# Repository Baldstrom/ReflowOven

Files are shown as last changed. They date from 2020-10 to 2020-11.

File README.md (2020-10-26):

# ReflowOven
A reflow oven controller designed in KiCAD, by Jaden Bottemiller

This project is designed to use an STM32 ARM Cortex-M4 microcontroller. 

All onboard devices interface to the microcontroller using I2C (with the exception of the SD Card Slot, which uses SPI). Also has a CAN interface, USB 2.0, and SWD. Features four seven segment displays, three buttons, and a rotary encoder with a custom logic circuit that interfaces with an I2C binary up/down counter to increment, decrement, and maintain accuracy of the relative position of the encoder.

Here is a rendering of the board with all of the parts modelled.
Some models from online resources or default in KiCAD, but many were made by me in Solidworks.

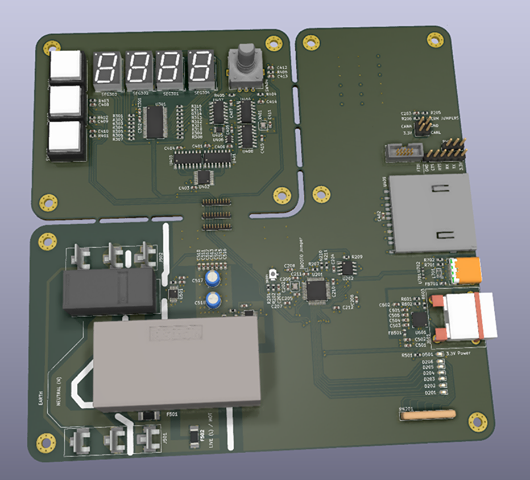
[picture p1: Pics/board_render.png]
Image of Board


The user interface portion of the board is able to be cut off so that it can be placed anywhere in a mechanical chassis for ease of construction.

Here is the board as seen by default in the KiCAD PCBnew Software.

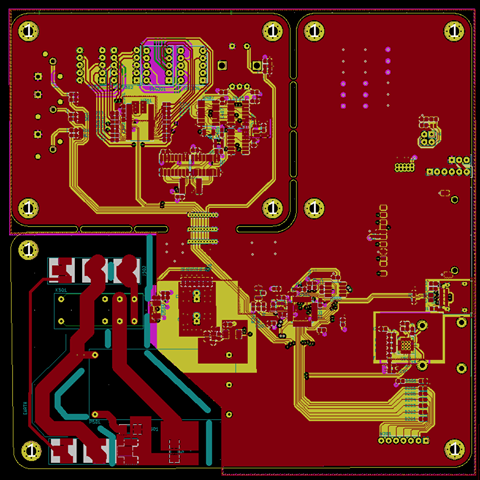
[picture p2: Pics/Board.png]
Image of PCBnew Render


A PDF of the Schematic Sheets can be found [here](https://github.com/Baldstrom/ReflowOven/blob/main/PDFs/ReflowOven.pdf).

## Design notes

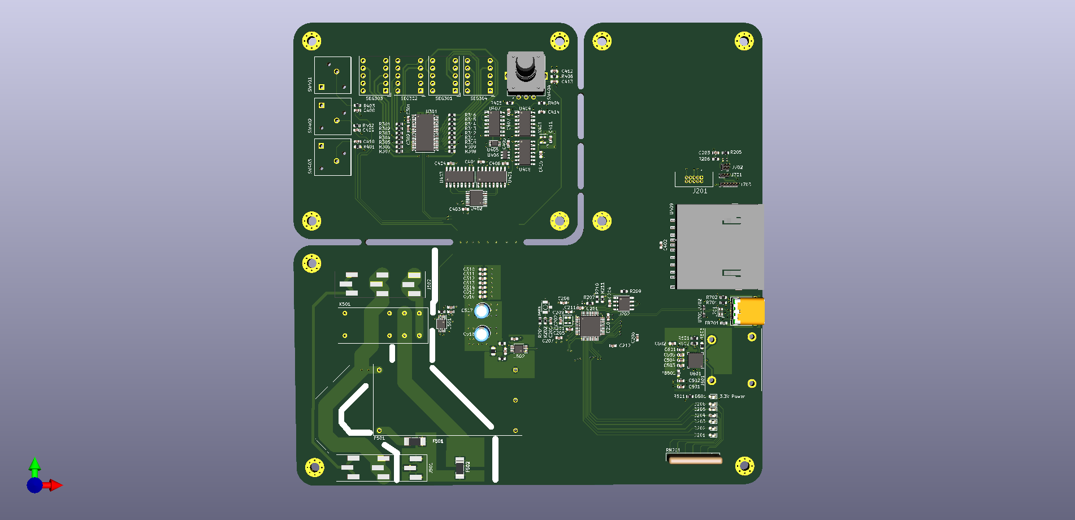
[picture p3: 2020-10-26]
Pics/ReflowOven.png

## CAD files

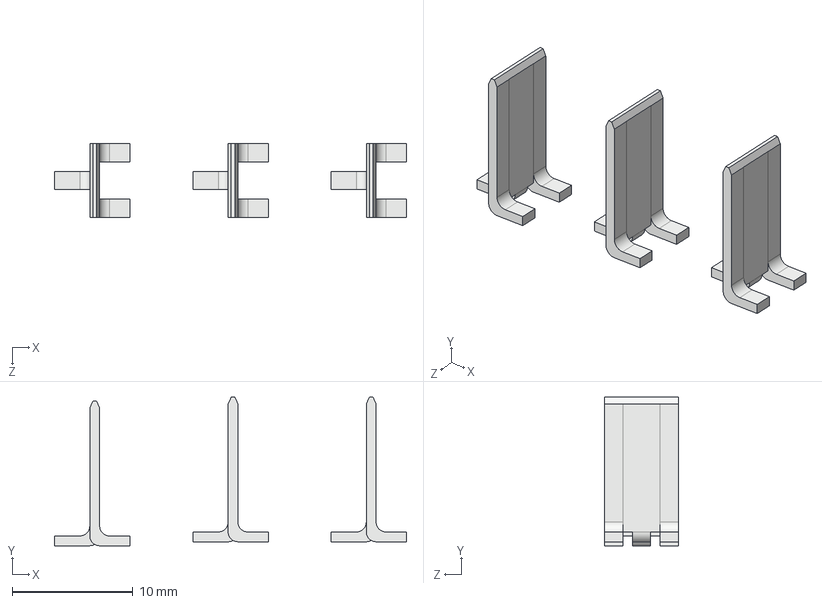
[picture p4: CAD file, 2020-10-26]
3D-Models/spade_connector_assy.STEP
29.1 x 12.3 x 6.10 mm
4928TR x 3

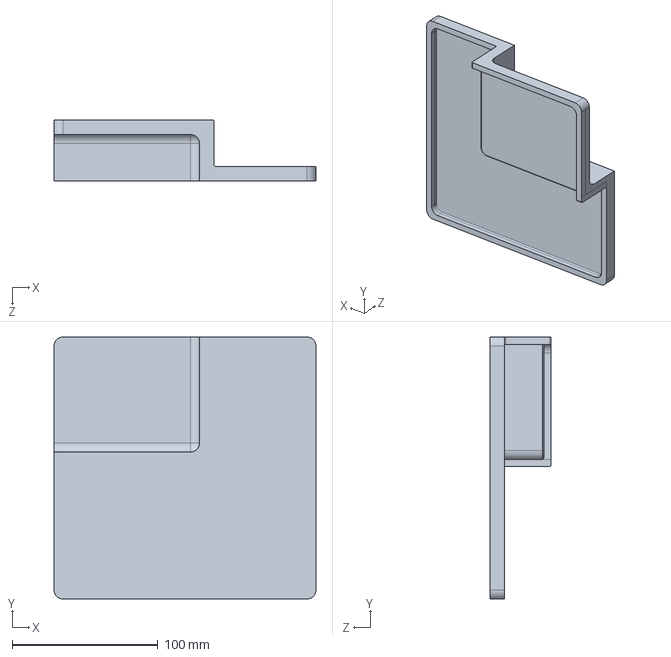
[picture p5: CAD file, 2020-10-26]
CAD/Chassis-Upper.SLDPRT
180.0 x 180.0 x 42.0 mm

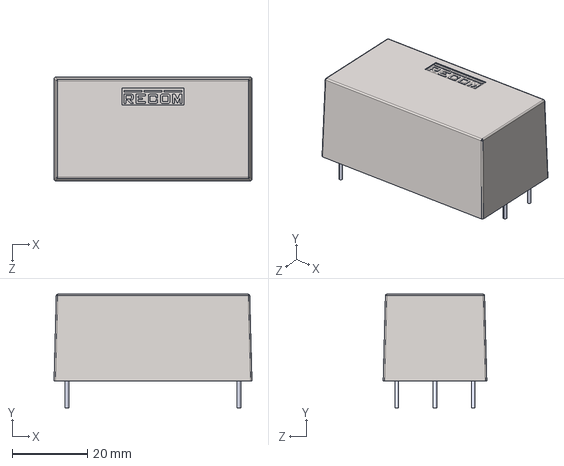
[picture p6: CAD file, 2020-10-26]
3D-Models/277.stp
52.7 x 30.2 x 27.6 mm

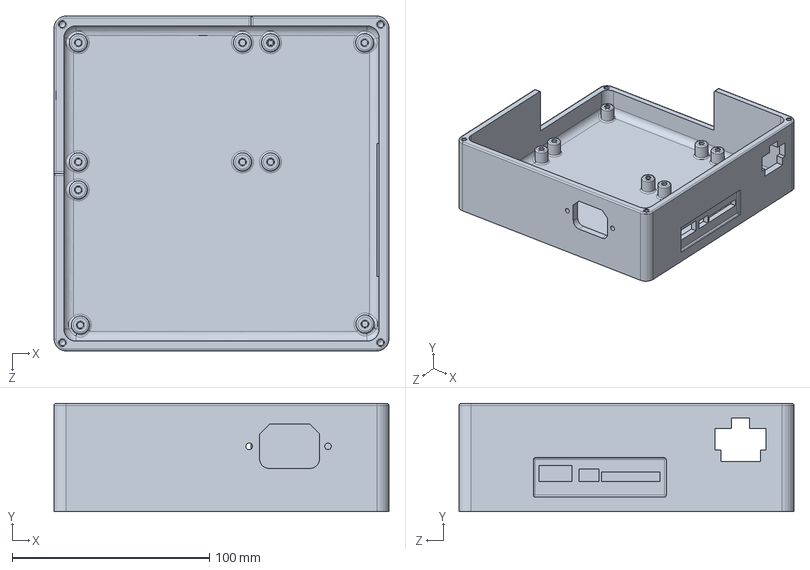
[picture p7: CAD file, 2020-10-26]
CAD/Chassis-Lower.SLDPRT
170.0 x 55.0 x 170.0 mm

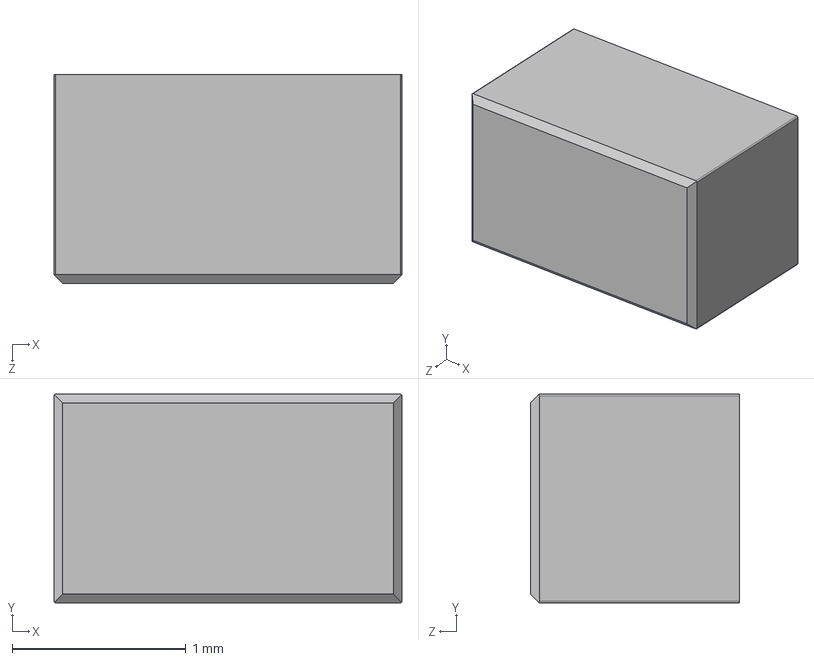
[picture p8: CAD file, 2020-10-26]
3D-Models/Choke.stl.STEP
2.00 x 1.20 x 1.20 mm

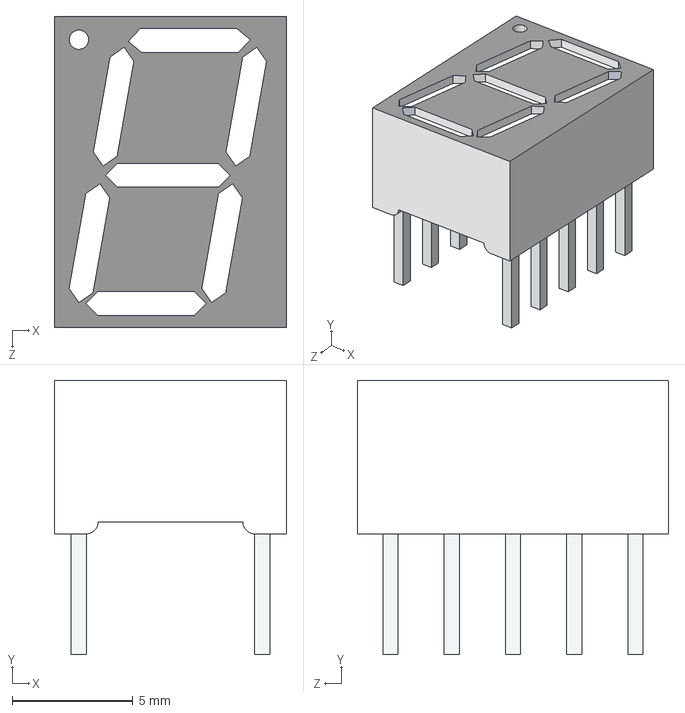
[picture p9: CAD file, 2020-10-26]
3D-Models/7seg.STEP
9.63 x 11.4 x 12.9 mm

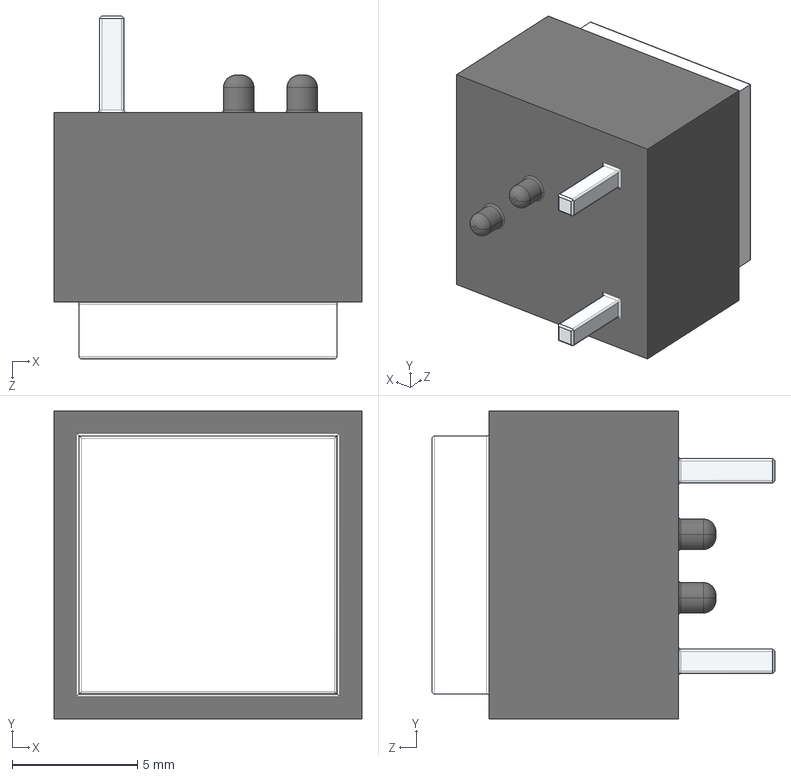
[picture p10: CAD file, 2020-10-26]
3D-Models/CKN4078-ND.STEP
12.3 x 12.3 x 13.7 mm

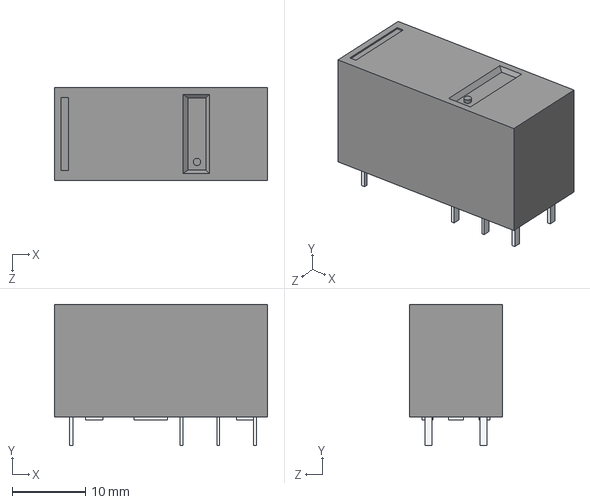
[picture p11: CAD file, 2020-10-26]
3D-Models/G5RL_U1_E.STEP
29.0 x 19.2 x 12.7 mm

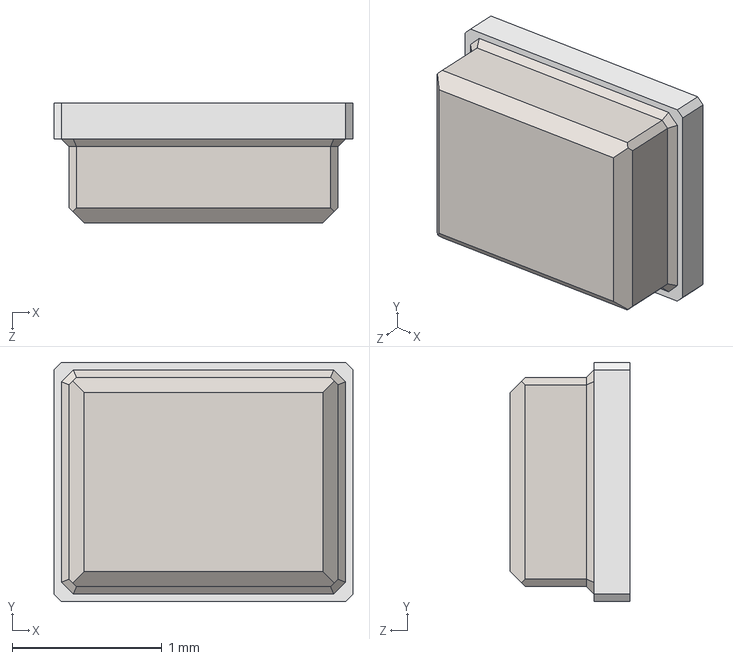
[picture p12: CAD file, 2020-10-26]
3D-Models/KC2016Z.stp
2.00 x 1.60 x 0.8 mm

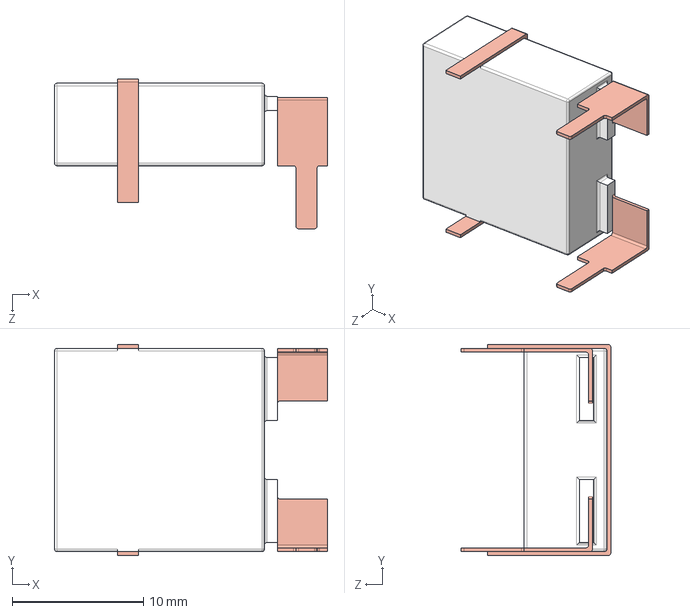
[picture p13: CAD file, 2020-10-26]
3D-Models/PRT-13612.stp
20.8 x 16.1 x 11.4 mm

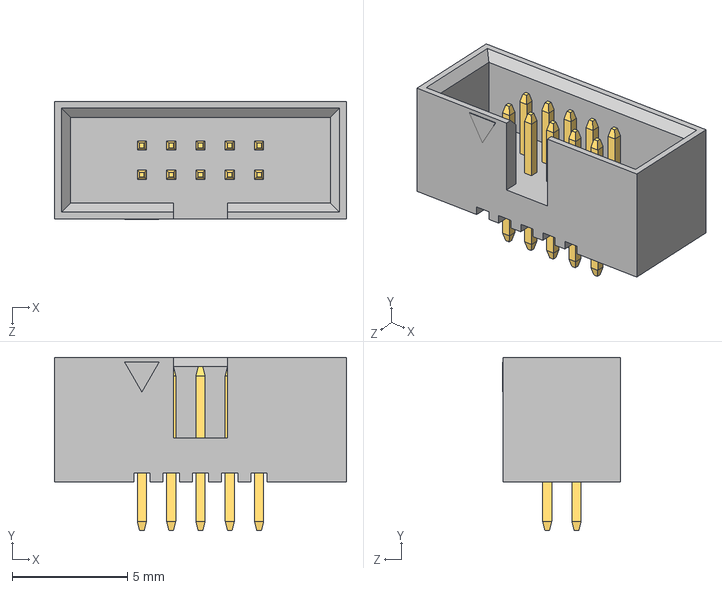
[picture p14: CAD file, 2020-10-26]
3D-Models/3220-10-0100.stp
12.7 x 7.50 x 5.13 mm

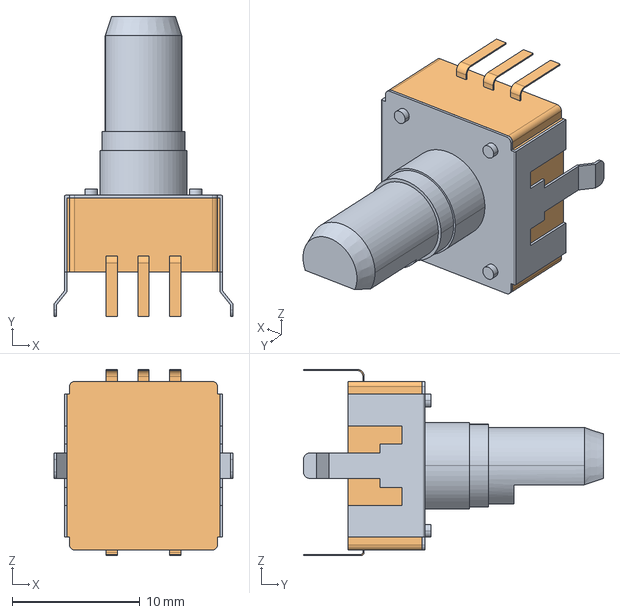
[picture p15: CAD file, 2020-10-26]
3D-Models/en12-hs22af20.stp
14.0 x 23.5 x 14.6 mm
BM-427
BM-428

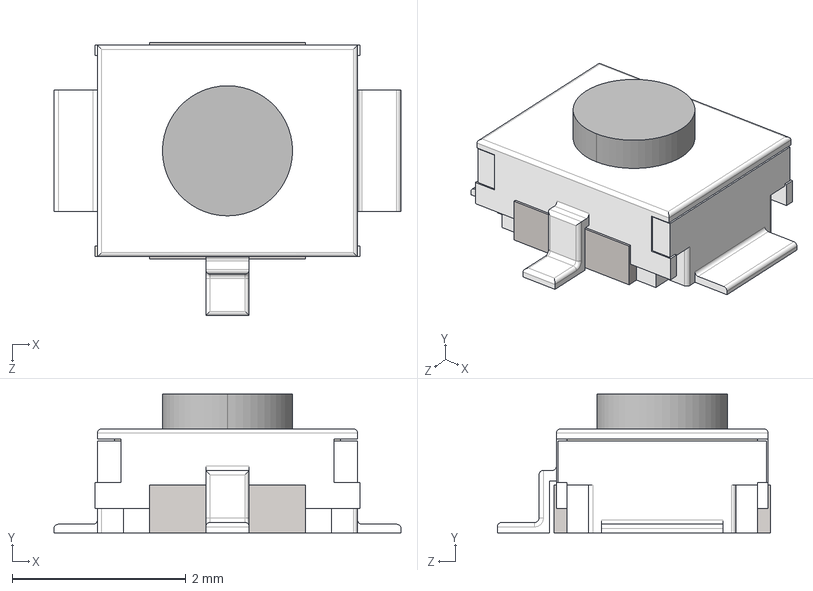
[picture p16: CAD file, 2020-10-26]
3D-Models/B3U-1100P--3DModel-STEP-1.stp
4.00 x 1.60 x 3.15 mm

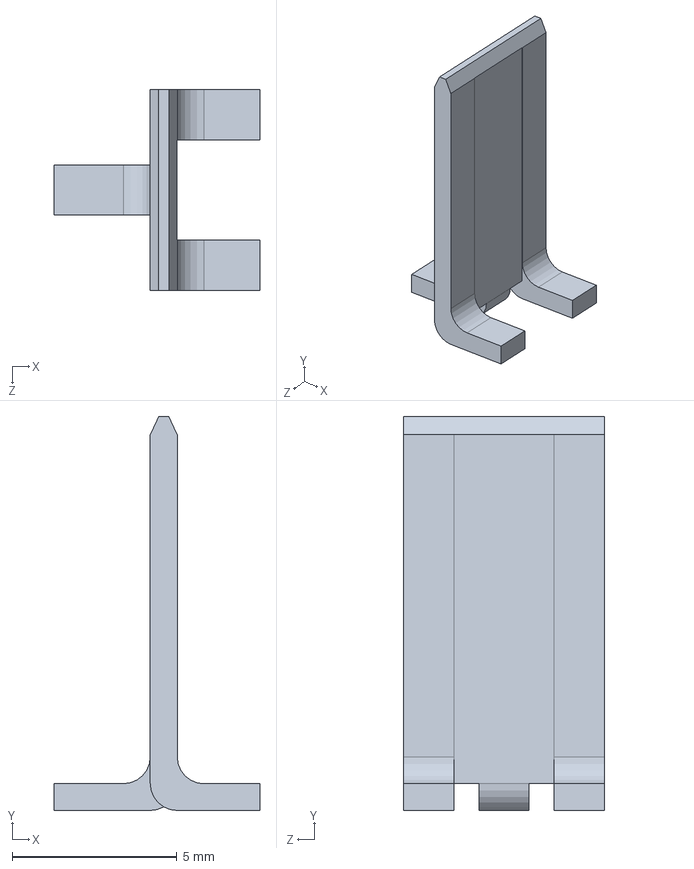
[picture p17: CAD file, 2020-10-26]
3D-Models/4928TR.SLDPRT
6.25 x 12.0 x 6.10 mm

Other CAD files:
Outputs/Mesh.stl
3D-Models/Choke.SLDPRT
3D-Models/10067847-001RLF.stp
3D-Models/277.SLDPRT
3D-Models/3220-10-0100.SLDPRT
3D-Models/7seg.SLDPRT
3D-Models/B3U-1100P--3DModel-STEP-1.SLDPRT
3D-Models/CKN4078-ND.SLDPRT
3D-Models/G5RL_U1_E.SLDPRT
3D-Models/KC2016Z.SLDPRT
3D-Models/PRT-13612.SLDPRT
3D-Models/PRT-13612.STL
3D-Models/spade_connector_assy.SLDASM
CAD/Chassis-Lower.STL
Gerber/ReflowOven-B_SilkS.dxf

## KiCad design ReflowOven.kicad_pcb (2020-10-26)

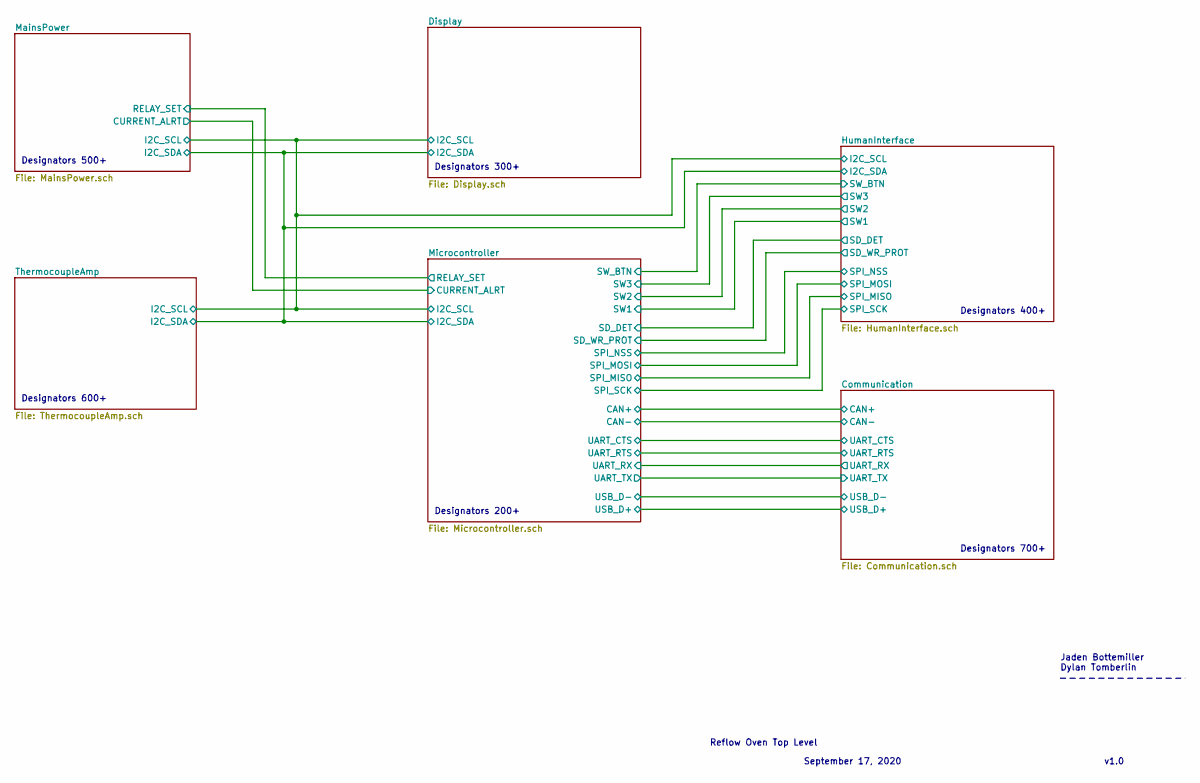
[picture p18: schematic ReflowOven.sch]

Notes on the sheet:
Reflow Oven Top Level
v1.0
September 17, 2020
Jaden Bottemiller Dylan Tomberlin
Designators 200+
Designators 600+
Designators 500+
Designators 300+
Designators 400+
Designators 700+

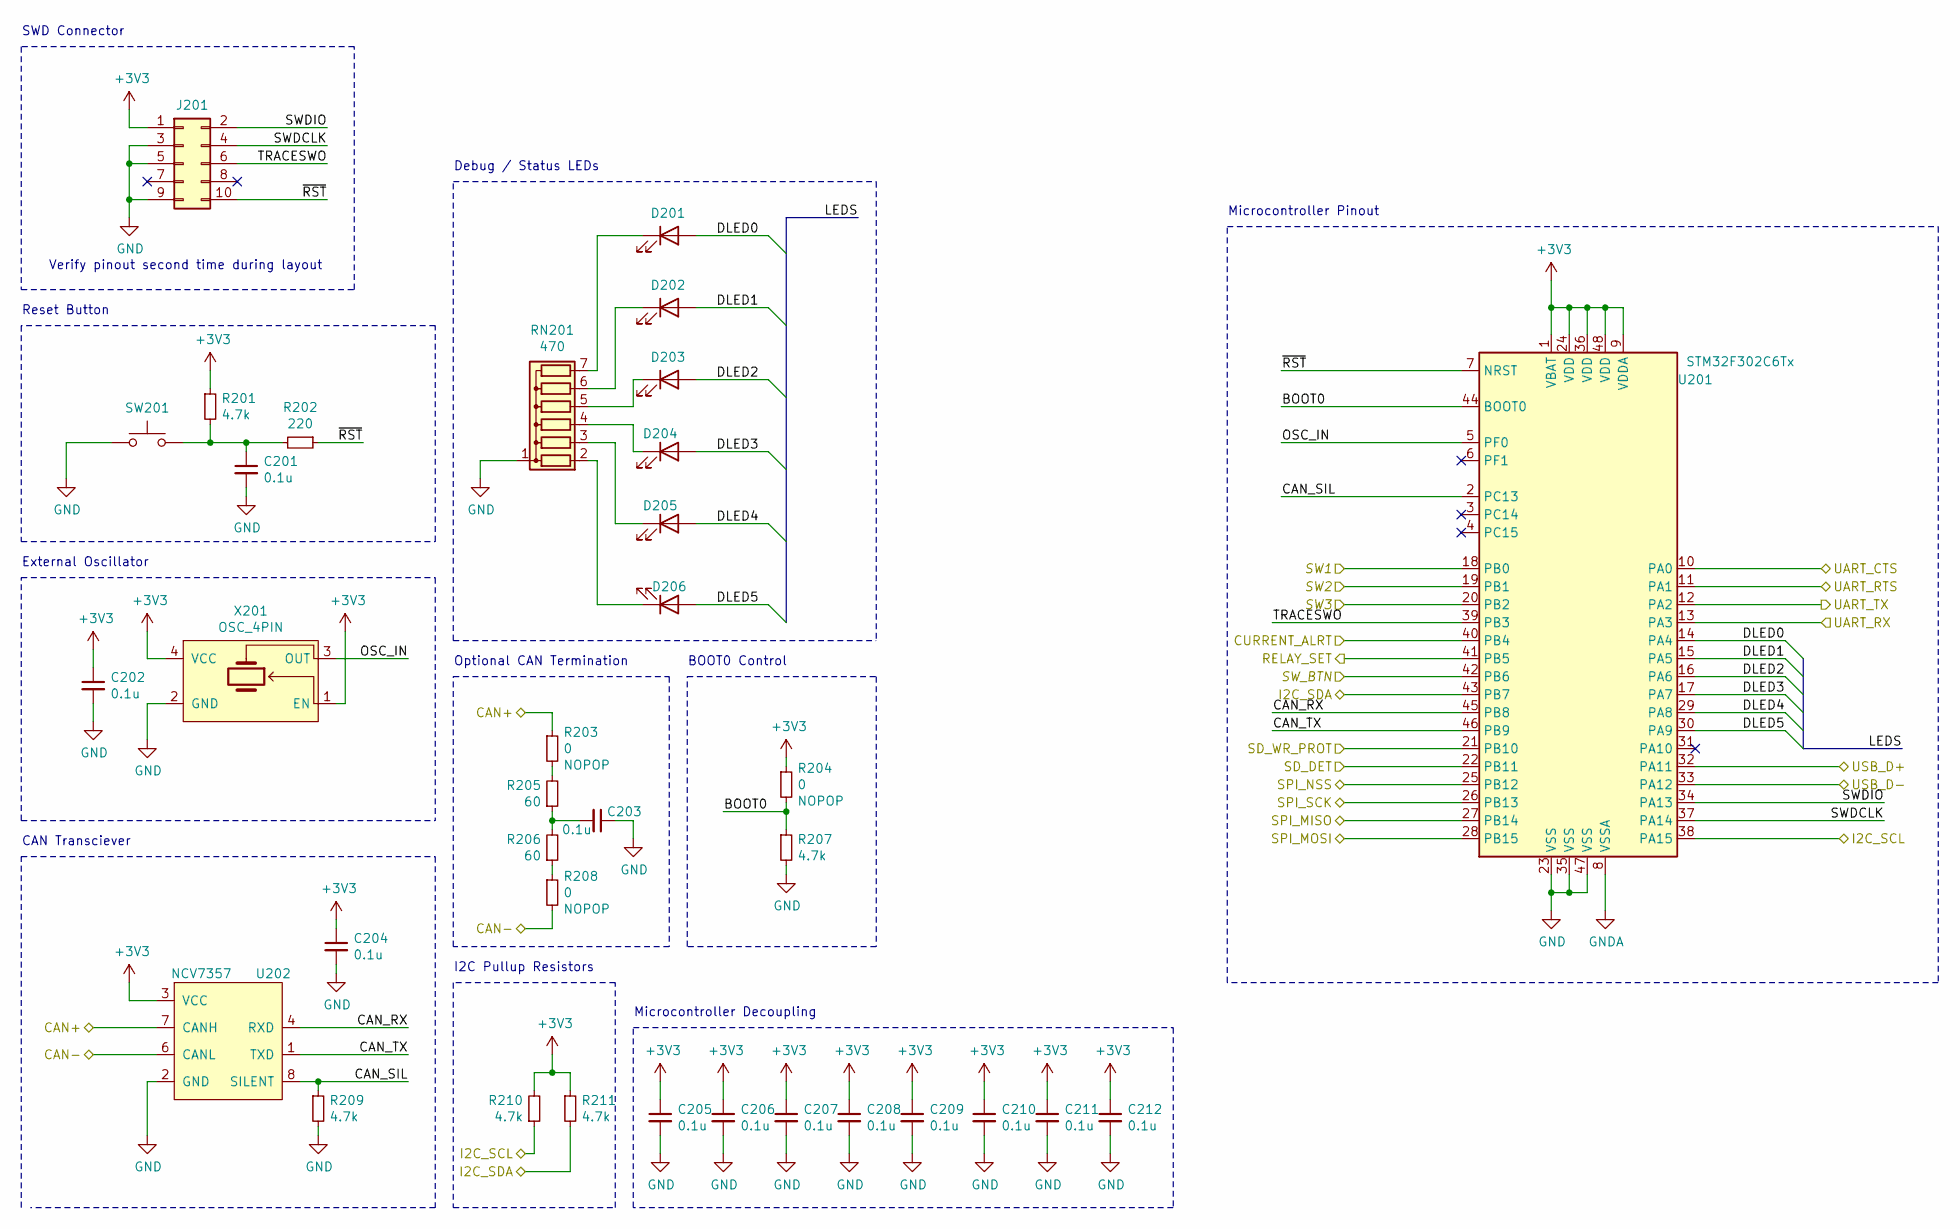
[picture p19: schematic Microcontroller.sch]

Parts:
C201, C202, C203, C204, C205, C206, C207, C208, C209, C210, C211, C212: 0.1u; C_0603_1608Metric
D201, D202, D203, D204, D205, D206: LED; LED_0603_1608Metric
J201: Conn_02x05_Odd_Even; CNC_3221-10-0100-00
R201, R207, R209, R210, R211: 4.7k; R_0603_1608Metric
R202: 220; R_0603_1608Metric
R203, R204, R208: 0; R_0201_0603Metric
R205, R206: 60; R_0603_1608Metric
RN201: 470; R_Array_SIP7
SW201: B3U-1100P; SW_B3U-1100P
U201: STM32F302C6Tx; LQFP-48_7x7mm_P0.5mm
U202: NCV7357; SOIC-8_3.9x4.9mm_P1.27mm
X201: OSC_4PIN; KC2016Z48.0000C15XXK

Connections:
/Communication/CAN+: R203.1, U202.7 (CANH); also elsewhere on the board
/Communication/CAN-: R208.2, U202.6 (CANL); also elsewhere on the board
/Communication/UART_CTS: U201.10 (PA0); also elsewhere on the board
/Communication/UART_RTS: U201.11 (PA1); also elsewhere on the board
/Communication/UART_RX: U201.13 (PA3); also elsewhere on the board
/Communication/UART_TX: U201.12 (PA2); also elsewhere on the board
/Communication/USB_D+: U201.32 (PA11); also elsewhere on the board
/Communication/USB_D-: U201.33 (PA12); also elsewhere on the board
/Display/I2C_SCL: R210.1, U201.38 (PA15); also elsewhere on the board
/Display/I2C_SDA: R211.2, U201.43 (PB7); also elsewhere on the board
/HumanInterface/SD_DET: U201.22 (PB11); also elsewhere on the board
/HumanInterface/SD_WR_PROT: U201.21 (PB10); also elsewhere on the board
/HumanInterface/SPI_MISO: U201.27 (PB14); also elsewhere on the board
/HumanInterface/SPI_MOSI: U201.28 (PB15); also elsewhere on the board
/HumanInterface/SPI_NSS: U201.25 (PB12); also elsewhere on the board
/HumanInterface/SPI_SCK: U201.26 (PB13); also elsewhere on the board
/HumanInterface/SW1: U201.18 (PB0); also elsewhere on the board
/HumanInterface/SW2: U201.19 (PB1); also elsewhere on the board
/HumanInterface/SW3: U201.20 (PB2); also elsewhere on the board
/HumanInterface/SW_BTN: U201.42 (PB6); also elsewhere on the board
/MainsPower/CURRENT_ALRT: U201.40 (PB4); also elsewhere on the board
/MainsPower/RELAY_SET: U201.41 (PB5); also elsewhere on the board
/Microcontroller/BOOT0: R204.2, R207.1, U201.44 (BOOT0)
/Microcontroller/CAN_RX: U201.45 (PB8), U202.4 (RXD)
/Microcontroller/CAN_SIL: R209.1, U201.2 (PC13), U202.8 (SILENT)
/Microcontroller/CAN_TX: U201.46 (PB9), U202.1 (TXD)
/Microcontroller/DLED0: D201.2 (A), U201.14 (PA4)
/Microcontroller/DLED1: D202.2 (A), U201.15 (PA5)
/Microcontroller/DLED2: D203.2 (A), U201.16 (PA6)
/Microcontroller/DLED3: D204.2 (A), U201.17 (PA7)
/Microcontroller/DLED4: D205.2 (A), U201.29 (PA8)
/Microcontroller/DLED5: D206.2 (A), U201.30 (PA9)
/Microcontroller/OSC_IN: U201.5 (PF0), X201.3 (OUT)
/Microcontroller/SWDCLK: J201.4, U201.37 (PA14)
/Microcontroller/SWDIO: J201.2, U201.34 (PA13)
/Microcontroller/TRACESWO: J201.6, U201.39 (PB3)
/Microcontroller/~RST: J201.10, R202.1, U201.7 (NRST)
GND: C201.2, C202.2, C203.1, C204.2, C205.2, C206.2, C207.2, C208.2, C209.2, C210.2, C211.2, C212.2, J201.3, J201.5, J201.9, R207.2, R209.2, RN201.1 (common), SW201.1, U201.8 (VSSA), U201.23 (VSS), U201.35 (VSS), U201.47 (VSS), U202.2 (GND), X201.2 (GND); also elsewhere on the board
unnamed: C201.1, R201.2, R202.2, SW201.2
unnamed: C203.2, R205.1, R206.2
unnamed: D201.1 (K), RN201.7 (R6)
unnamed: D202.1 (K), RN201.6 (R5)
unnamed: D203.1 (K), RN201.5 (R4)
unnamed: D204.1 (K), RN201.4 (R3)
unnamed: D205.1 (K), RN201.3 (R2)
unnamed: D206.1 (K), RN201.2 (R1)
unnamed: R203.2, R205.2
unnamed: R206.1, R208.1

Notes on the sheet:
Microcontroller Decoupling
Microcontroller Pinout
CAN Transciever
I2C Pullup Resistors
External Oscillator
Verify pinout second time during layout
SWD Connector
Reset Button
BOOT0 Control
Optional CAN Termination
Debug / Status LEDs

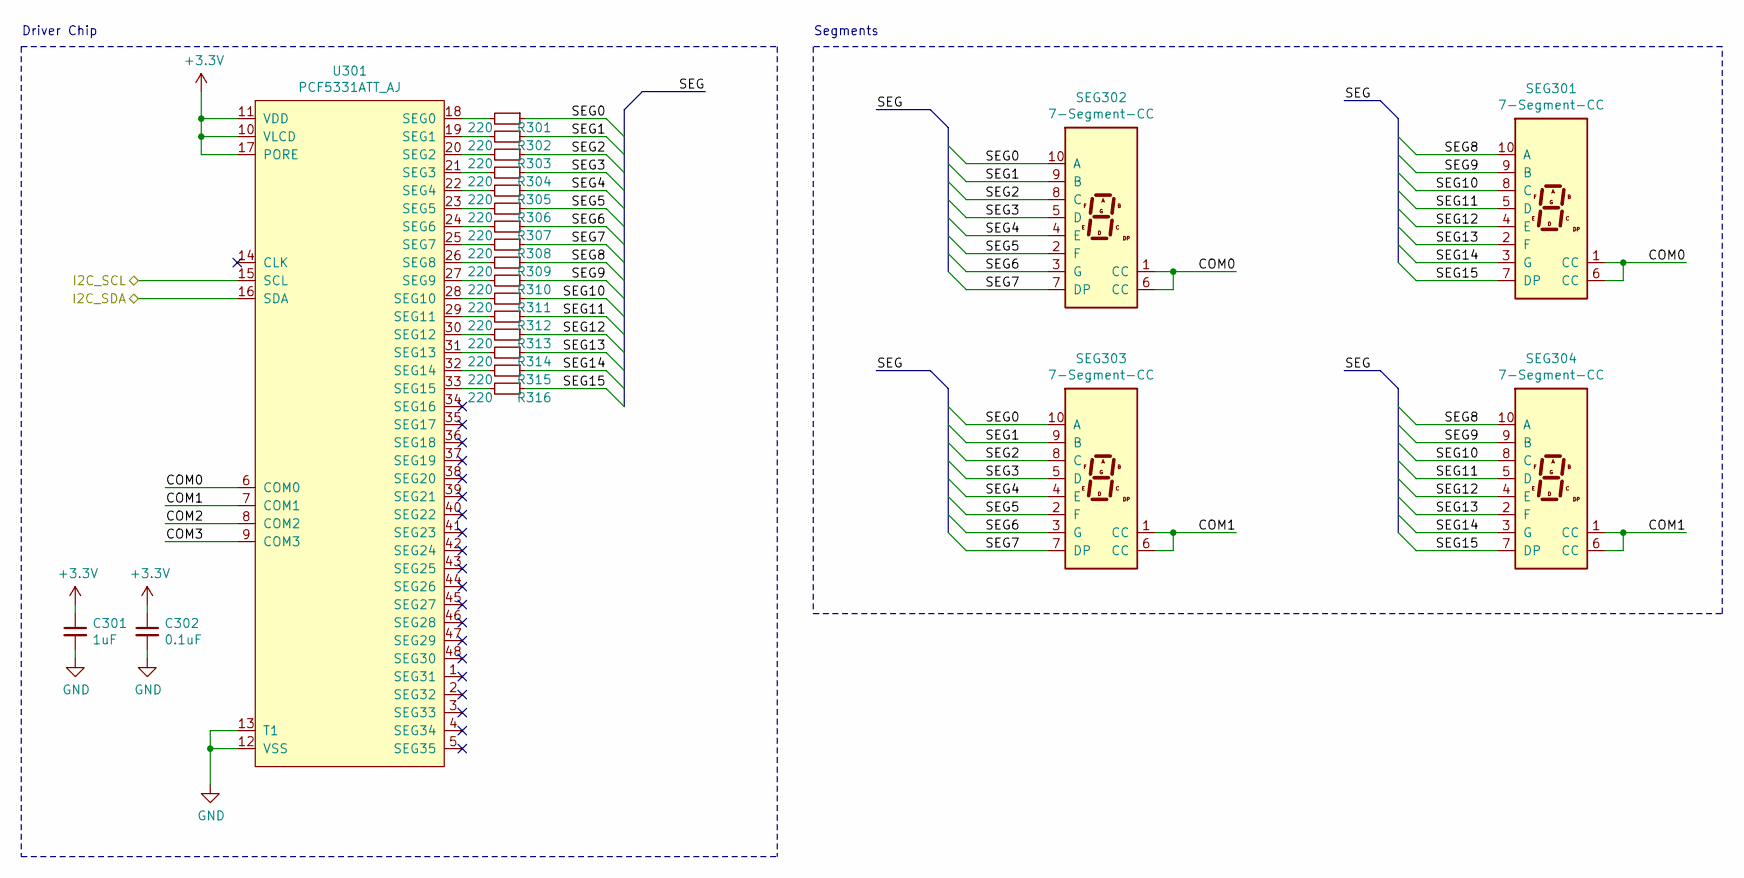
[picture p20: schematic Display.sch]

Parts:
C301: 1uF; C_0603_1608Metric
C302: 0.1uF; C_0603_1608Metric
R301, R302, R303, R304, R305, R306, R307, R308, R309, R310, R311, R312, R313, R314, R315, R316: 220; R_0603_1608Metric
SEG301, SEG302, SEG303, SEG304: 7-Segment-CC; Sx39-1xxxxx
U301: PCF5331ATT_AJ; TSSOP-48_6.1x12.5mm_P0.5mm

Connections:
/Display/COM0: SEG301.1 (CC), SEG301.6 (CC), SEG302.1 (CC), SEG302.6 (CC), U301.6 (COM0)
/Display/COM1: SEG303.1 (CC), SEG303.6 (CC), SEG304.1 (CC), SEG304.6 (CC), U301.7 (COM1)
/Display/COM2: U301.8 (COM2)
/Display/COM3: U301.9 (COM3)
/Display/I2C_SCL: U301.15 (SCL); also elsewhere on the board
/Display/I2C_SDA: U301.16 (SDA); also elsewhere on the board
/Display/SEG0: R301.1, SEG302.10 (A), SEG303.10 (A)
/Display/SEG1: R302.1, SEG302.9 (B), SEG303.9 (B)
/Display/SEG2: R303.1, SEG302.8 (C), SEG303.8 (C)
/Display/SEG3: R304.1, SEG302.5 (D), SEG303.5 (D)
/Display/SEG4: R305.1, SEG302.4 (E), SEG303.4 (E)
/Display/SEG5: R306.1, SEG302.2 (F), SEG303.2 (F)
/Display/SEG6: R307.1, SEG302.3 (G), SEG303.3 (G)
/Display/SEG7: R308.1, SEG302.7 (DP), SEG303.7 (DP)
/Display/SEG8: R309.1, SEG301.10 (A), SEG304.10 (A)
/Display/SEG9: R310.1, SEG301.9 (B), SEG304.9 (B)
/Display/SEG10: R311.1, SEG301.8 (C), SEG304.8 (C)
/Display/SEG11: R312.1, SEG301.5 (D), SEG304.5 (D)
/Display/SEG12: R313.1, SEG301.4 (E), SEG304.4 (E)
/Display/SEG13: R314.1, SEG301.2 (F), SEG304.2 (F)
/Display/SEG14: R315.1, SEG301.3 (G), SEG304.3 (G)
/Display/SEG15: R316.1, SEG301.7 (DP), SEG304.7 (DP)
GND: C301.2, C302.2, U301.12 (VSS), U301.13 (T1); also elsewhere on the board
unnamed: R301.2, U301.18 (SEG0)
unnamed: R302.2, U301.19 (SEG1)
unnamed: R303.2, U301.20 (SEG2)
unnamed: R304.2, U301.21 (SEG3)
unnamed: R305.2, U301.22 (SEG4)
unnamed: R306.2, U301.23 (SEG5)
unnamed: R307.2, U301.24 (SEG6)
unnamed: R308.2, U301.25 (SEG7)
unnamed: R309.2, U301.26 (SEG8)
unnamed: R310.2, U301.27 (SEG9)
unnamed: R311.2, U301.28 (SEG10)
unnamed: R312.2, U301.29 (SEG11)
unnamed: R313.2, U301.30 (SEG12)
unnamed: R314.2, U301.31 (SEG13)
unnamed: R315.2, U301.32 (SEG14)
unnamed: R316.2, U301.33 (SEG15)

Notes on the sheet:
Driver Chip
Segments

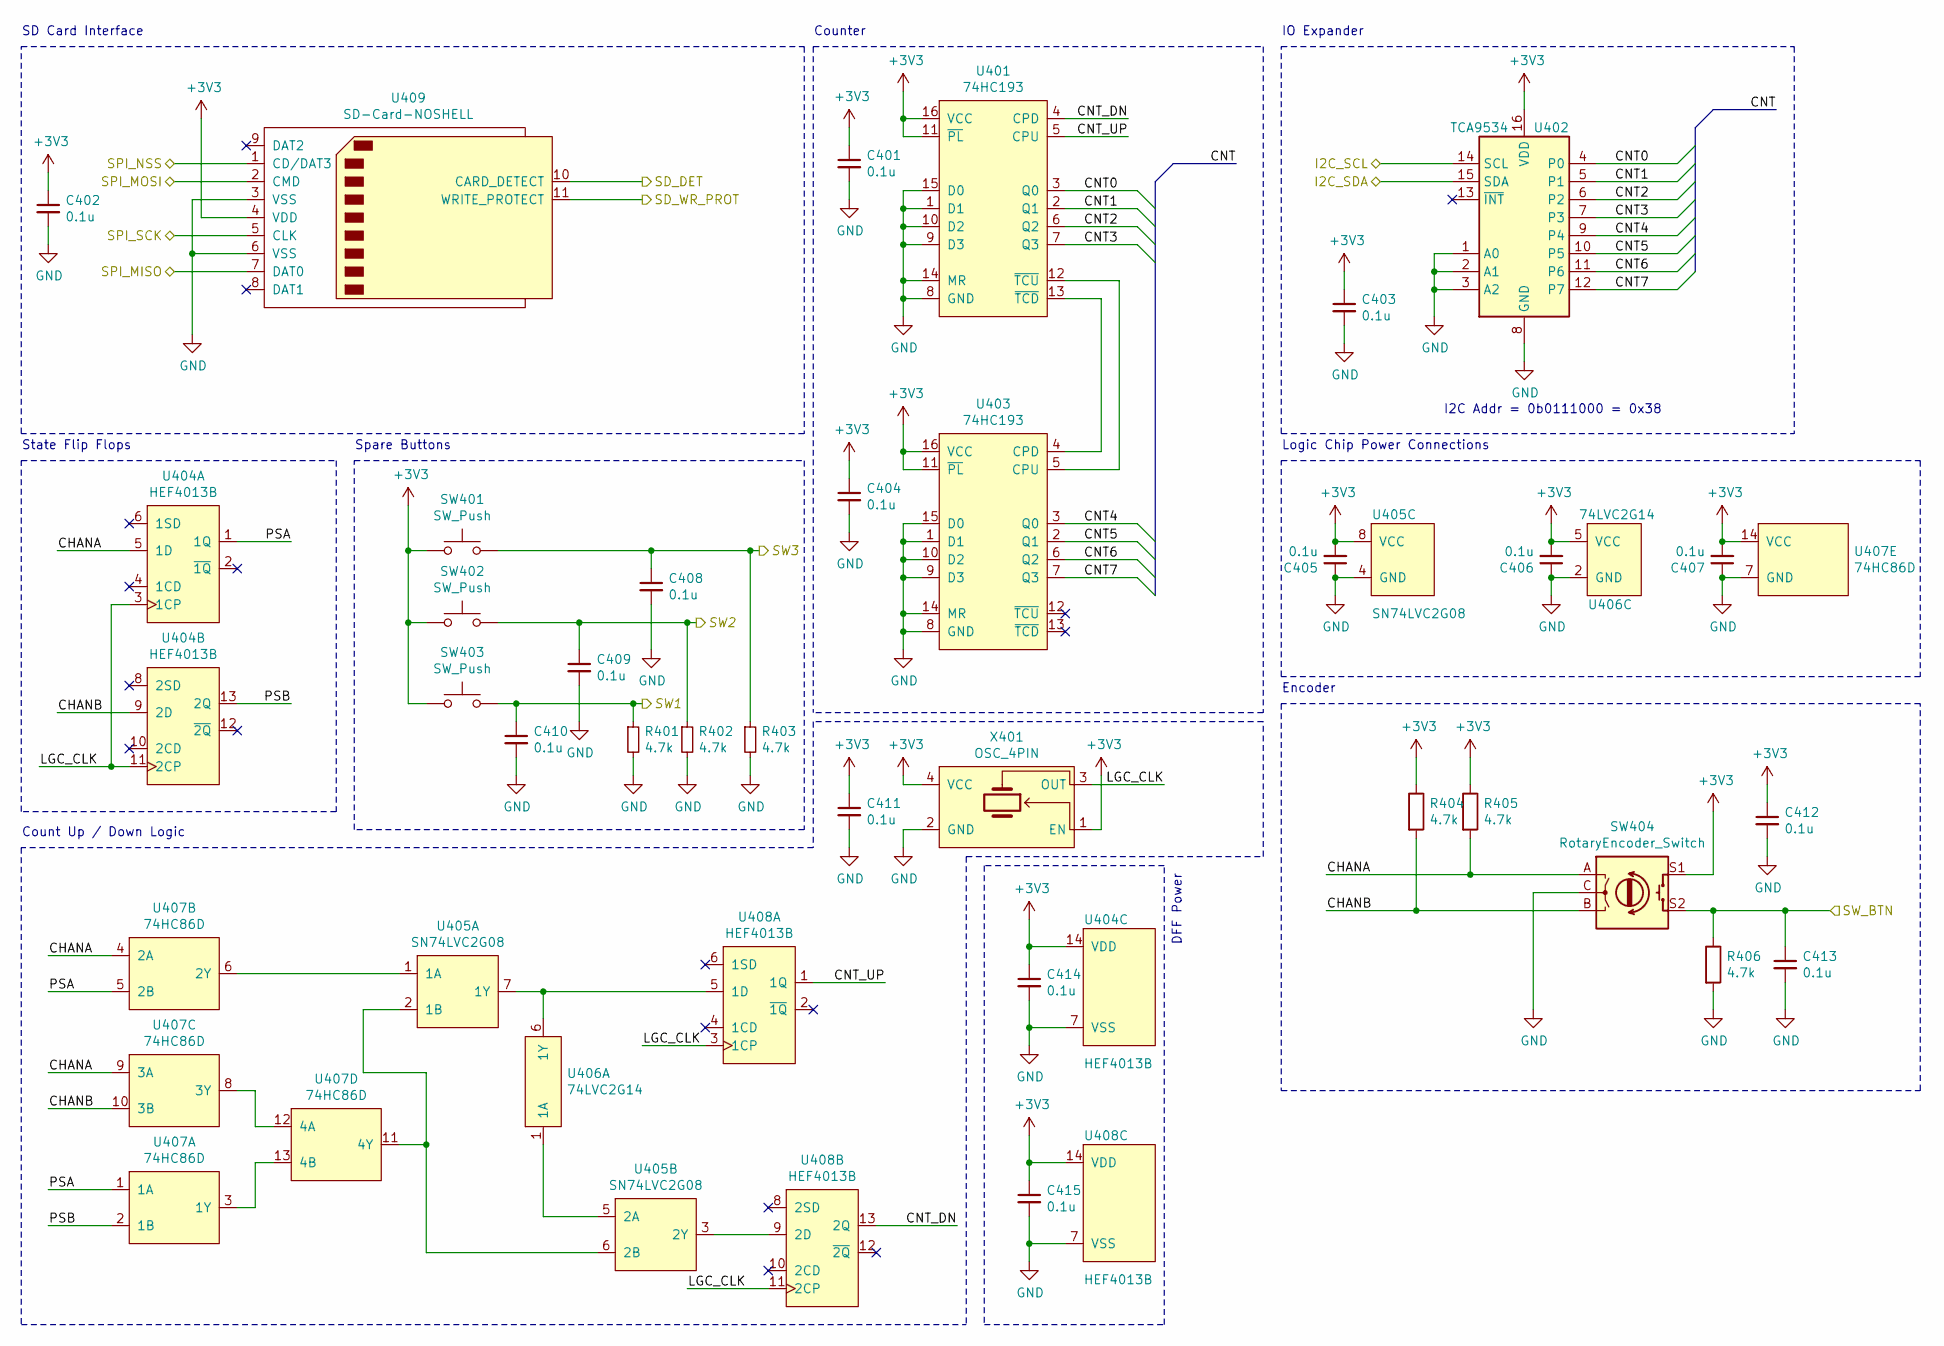
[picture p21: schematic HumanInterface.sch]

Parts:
C401, C402, C403, C404, C405, C406, C407, C408, C409, C410, C411, C412, C413, C414, C415: 0.1u; C_0603_1608Metric
R401, R402, R403, R404, R405, R406: 4.7k; R_0603_1608Metric
SW401, SW402, SW403: SW_Push; SW_KS11R21CQD
SW404: RotaryEncoder_Switch; EN12-HS22AF20
U401, U403: 74HC193; SOIC-16_3.9x9.9mm_P1.27mm
U402: TCA9534; TSSOP-16_4.4x5mm_P0.65mm
U404, U408: HEF4013B; SOIC-14_3.9x8.7mm_P1.27mm
U405: SN74LVC2G08; VSSOP-8_2.3x2mm_P0.5mm
U406: 74LVC2G14; TSOP-6_1.65x3.05mm_P0.95mm
U407: 74HC86D; SOIC-14_3.9x8.7mm_P1.27mm
U409: SD-Card-NOSHELL; AMPHENOL-10067847
X401: OSC_4PIN; KC2016Z48.0000C15XXK

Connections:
/Display/I2C_SCL: U402.14 (SCL); also elsewhere on the board
/Display/I2C_SDA: U402.15 (SDA); also elsewhere on the board
/HumanInterface/CHANA: R405.2, SW404.A, U404.5 (1D), U407.4 (2A), U407.9 (3A)
/HumanInterface/CHANB: R404.2, SW404.B, U404.9 (2D), U407.10 (3B)
/HumanInterface/CNT0: U401.3 (Q0), U402.4 (P0)
/HumanInterface/CNT1: U401.2 (Q1), U402.5 (P1)
/HumanInterface/CNT2: U401.6 (Q2), U402.6 (P2)
/HumanInterface/CNT3: U401.7 (Q3), U402.7 (P3)
/HumanInterface/CNT4: U402.9 (P4), U403.3 (Q0)
/HumanInterface/CNT5: U402.10 (P5), U403.2 (Q1)
/HumanInterface/CNT6: U402.11 (P6), U403.6 (Q2)
/HumanInterface/CNT7: U402.12 (P7), U403.7 (Q3)
/HumanInterface/CNT_DN: U401.4 (CPD), U408.13 (2Q)
/HumanInterface/CNT_UP: U401.5 (CPU), U408.1 (1Q)
/HumanInterface/LGC_CLK: U404.3 (1CP), U404.11 (2CP), U408.3 (1CP), U408.11 (2CP), X401.3 (OUT)
/HumanInterface/PSA: U404.1 (1Q), U407.1 (1A), U407.5 (2B)
/HumanInterface/PSB: U404.13 (2Q), U407.2 (1B)
/HumanInterface/SD_DET: U409.10 (CARD_DETECT); also elsewhere on the board
/HumanInterface/SD_WR_PROT: U409.11 (WRITE_PROTECT); also elsewhere on the board
/HumanInterface/SPI_MISO: U409.7 (DAT0); also elsewhere on the board
/HumanInterface/SPI_MOSI: U409.2 (CMD); also elsewhere on the board
/HumanInterface/SPI_NSS: U409.1 (CD/DAT3); also elsewhere on the board
/HumanInterface/SPI_SCK: U409.5 (CLK); also elsewhere on the board
/HumanInterface/SW1: C410.1, R401.1, SW403.2; also elsewhere on the board
/HumanInterface/SW2: C409.1, R402.1, SW402.2; also elsewhere on the board
/HumanInterface/SW3: C408.1, R403.1, SW401.2; also elsewhere on the board
/HumanInterface/SW_BTN: C413.1, R406.1, SW404.S2; also elsewhere on the board
GND: C401.2, C402.2, C403.2, C404.2, C405.1, C406.1, C407.1, C408.2, C409.2, C410.2, C411.2, C412.2, C413.2, C414.2, C415.2, R401.2, R402.2, R403.2, R406.2, SW404.C, U401.1 (D1), U401.8 (GND), U401.9 (D3), U401.10 (D2), U401.14 (MR), U401.15 (D0), U402.1 (A0), U402.2 (A1), U402.3 (A2), U402.8 (GND), U403.1 (D1), U403.8 (GND), U403.9 (D3), U403.10 (D2), U403.14 (MR), U403.15 (D0), U404.7 (VSS), U405.4 (GND), U406.2 (GND), U407.7 (GND), U408.7 (VSS), U409.3 (VSS), U409.6 (VSS), U409.GND, X401.2 (GND); also elsewhere on the board
unnamed: U401.12 (~TCU), U403.5 (CPU)
unnamed: U401.13 (~TCD), U403.4 (CPD)
unnamed: U405.1 (1A), U407.6 (2Y)
unnamed: U405.2 (1B), U405.6 (2B), U407.11 (4Y)
unnamed: U405.3 (2Y), U408.9 (2D)
unnamed: U405.5 (2A), U406.1 (1A)
unnamed: U405.7 (1Y), U406.6 (1Y), U408.5 (1D)
unnamed: U407.8 (3Y), U407.12 (4A)
unnamed: U407.3 (1Y), U407.13 (4B)

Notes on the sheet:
SD Card Interface
Encoder
Counter
State Flip Flops
Count Up / Down Logic
Logic Chip Power Connections
IO Expander
Spare Buttons
I2C Addr = 0b0111000 = 0x38
DFF Power

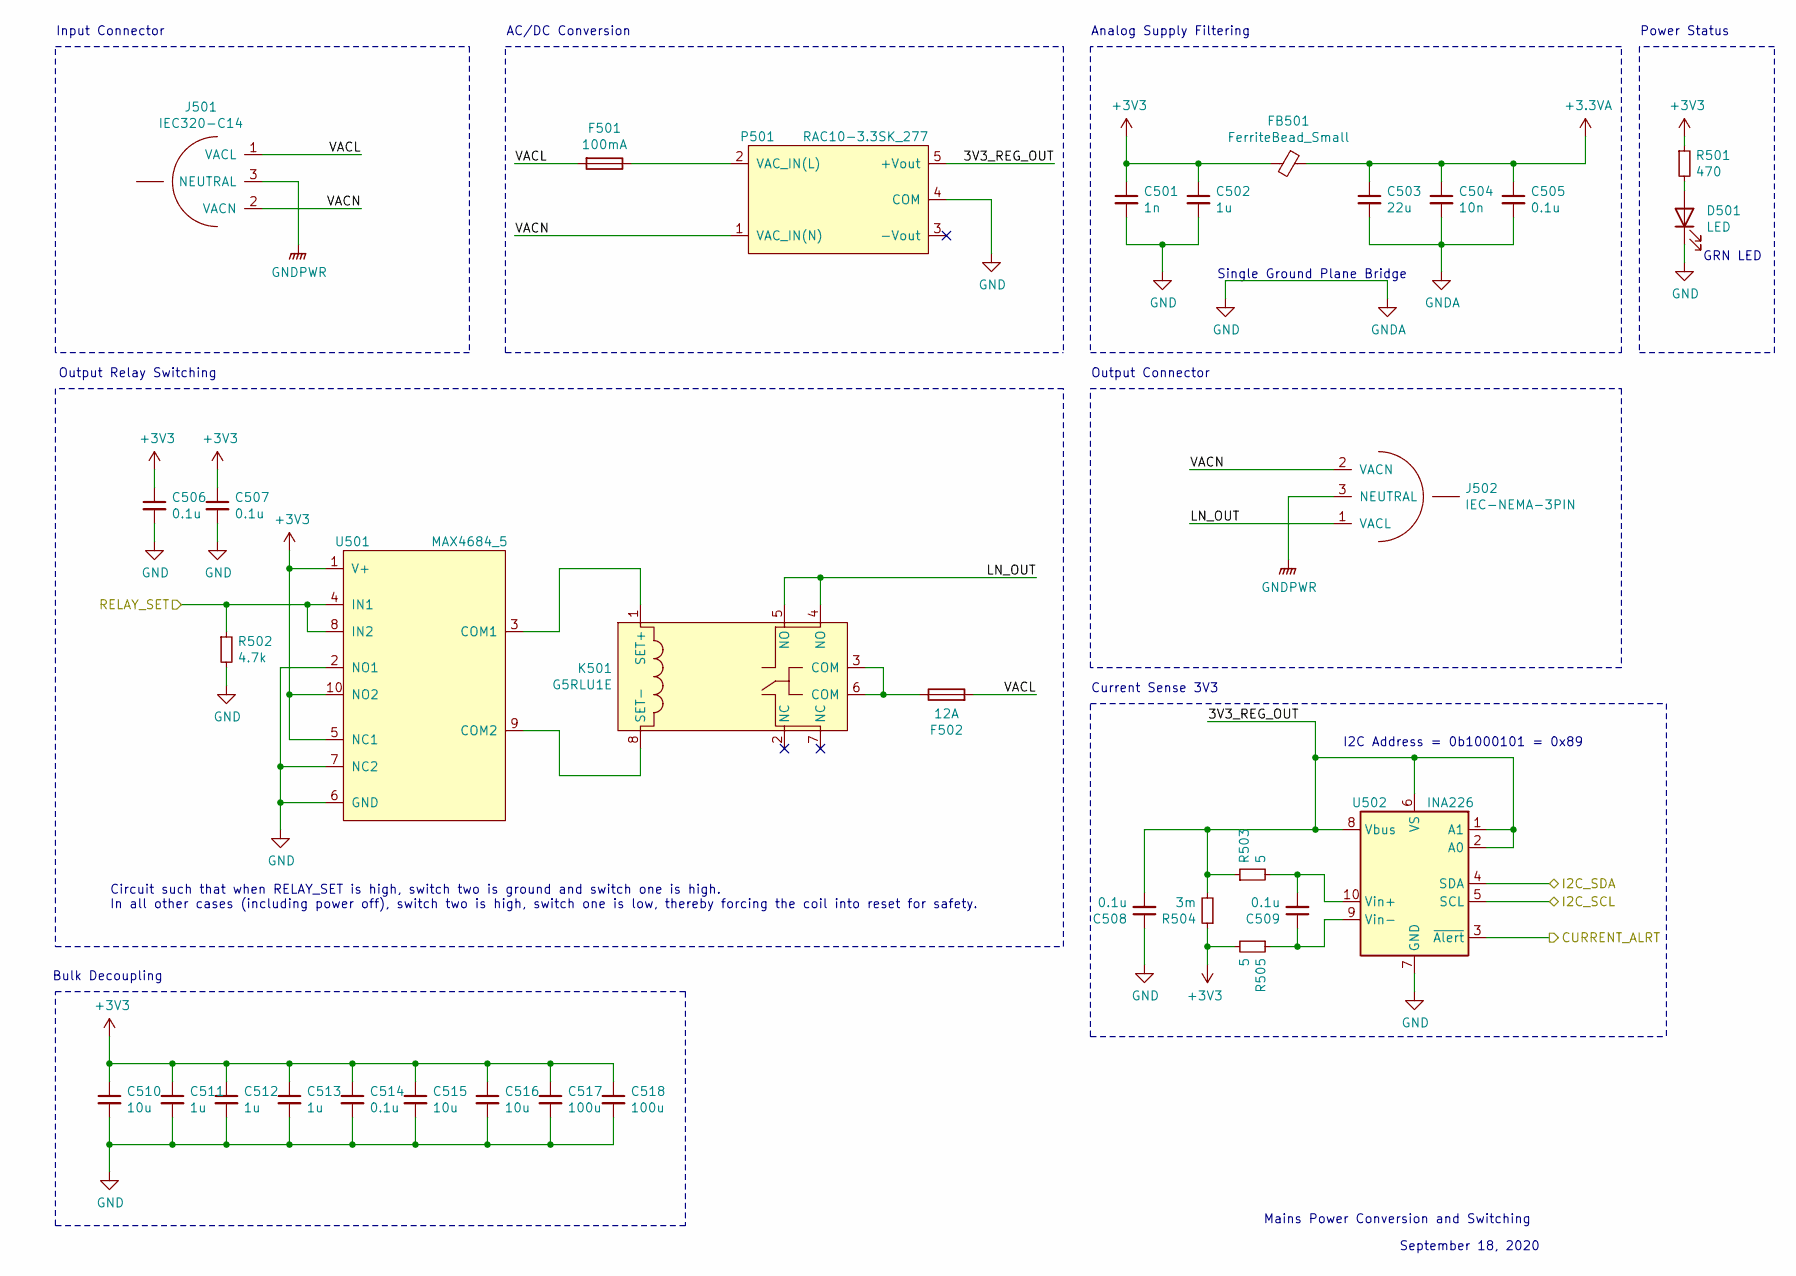
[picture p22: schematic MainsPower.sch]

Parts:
C501: 1n; C_0603_1608Metric
C502, C511, C512, C513: 1u; C_0603_1608Metric
C503: 22u; C_0603_1608Metric
C504: 10n; C_0603_1608Metric
C505, C506, C507, C508, C509, C514: 0.1u; C_0603_1608Metric
C510, C515, C516: 10u; C_0603_1608Metric
C517, C518: 100u; CP_Radial_D5.0mm_P2.00mm
D501: LED; LED_0603_1608Metric
F501: 100mA; FUSC6125X279N
F502: 12A; FUSC6125X279N
FB501: FerriteBead_Small; L_0603_1608Metric
J501: IEC320-C14; 3x1-0.24in-Spade-SMD
J502: IEC-NEMA-3PIN; 3x1-0.24in-Spade-SMD
K501: G5RLU1E; G5RLU-1-E DC3
P501: RAC10-3.3SK_277; RAC10-3.3SK-277
R501: 470; R_0603_1608Metric
R502: 4.7k; R_0603_1608Metric
R503, R505: 5; R_0603_1608Metric
R504: 3m; R_0805_2012Metric
U501: MAX4684_5; MSOP-10_3x3mm_P0.5mm
U502: INA226; MSOP-10_3x3mm_P0.5mm

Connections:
+3.3VA: C503.1, C504.1, C505.1, FB501.1; also elsewhere on the board
/Display/I2C_SCL: U502.5 (SCL); also elsewhere on the board
/Display/I2C_SDA: U502.4 (SDA); also elsewhere on the board
/MainsPower/3V3_REG_OUT: C508.2, P501.5 (+Vout), R503.1, R504.2, U502.1 (A1), U502.2 (A0), U502.6 (VS), U502.8 (Vbus)
/MainsPower/CURRENT_ALRT: U502.3 (~Alert~); also elsewhere on the board
/MainsPower/LN_OUT: J502.1 (VACL), K501.4 (NO), K501.5 (NO)
/MainsPower/RELAY_SET: R502.1, U501.4 (IN1), U501.8 (IN2); also elsewhere on the board
/MainsPower/VACL: F501.2, F502.2, J501.1 (VACL)
/MainsPower/VACN: J501.2 (VACN), J502.2 (VACN), P501.1 (VAC_IN(N))
GND: C501.2, C502.2, C503.2, C504.2, C505.2, C506.2, C507.2, C508.1, C510.2, C511.2, C512.2, C513.2, C514.2, C515.2, C516.2, C517.2, C518.2, D501.1 (K), P501.4 (COM), R502.2, U501.2 (NO1), U501.6 (GND), U501.7 (NC2), U502.7 (GND); also elsewhere on the board
GNDPWR: J501.3 (NEUTRAL), J502.3 (NEUTRAL)
unnamed: C509.1, R505.1, U502.9 (Vin-)
unnamed: C509.2, R503.2, U502.10 (Vin+)
unnamed: D501.2 (A), R501.2
unnamed: F501.1, P501.2 (VAC_IN(L))
unnamed: F502.1, K501.3 (COM), K501.6 (COM)
unnamed: K501.1 (SET+), U501.3 (COM1)
unnamed: K501.8 (SET-), U501.9 (COM2)

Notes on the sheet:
Bulk Decoupling
AC/DC Conversion
Mains Power Conversion and Switching
September 18, 2020
Circuit such that when RELAY_SET is high, switch two is ground and switch one is high. In all other cases (including power off), switch two is high, switch one is low, thereby forcing the coil into reset for safety.
Output Relay Switching
Input Connector
Output Connector
Analog Supply Filtering
Single Ground Plane Bridge
Current Sense 3V3
I2C Address = 0b1000101 = 0x89
GRN LED
Power Status

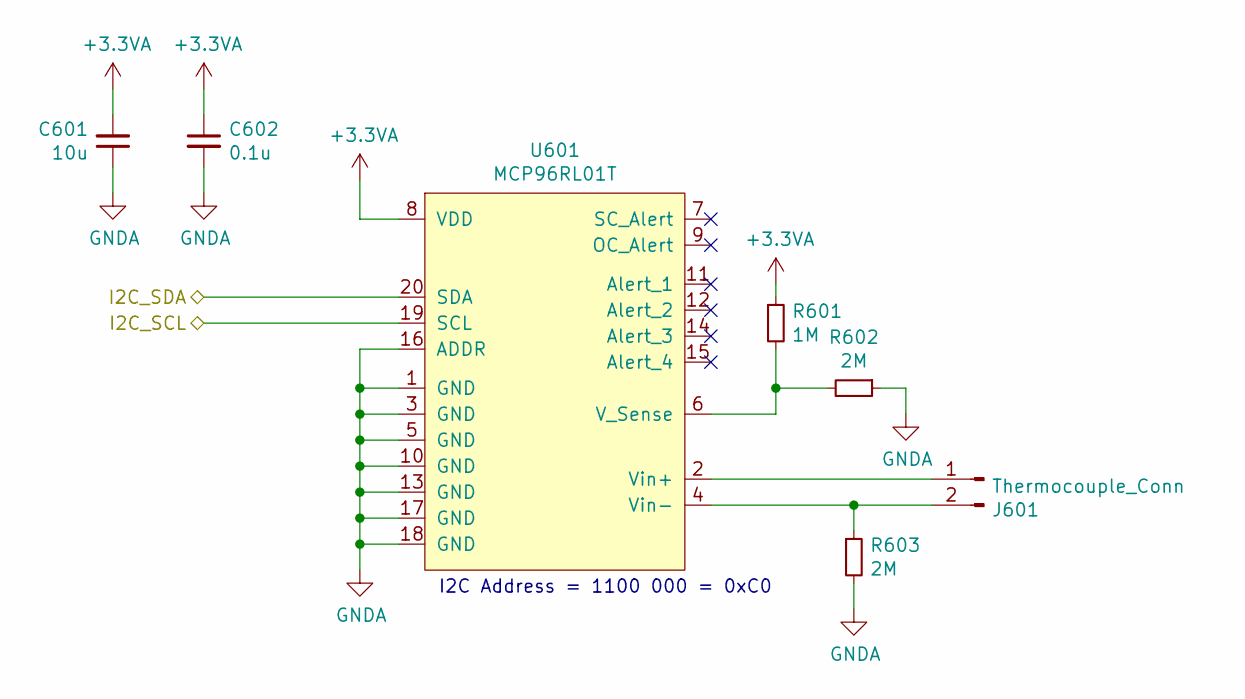
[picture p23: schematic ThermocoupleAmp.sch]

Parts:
C601: 10u; C_0603_1608Metric
C602: 0.1u; C_0603_1608Metric
J601: Thermocouple_Conn; PRT-13612
R601: 1M; R_0603_1608Metric
R602, R603: 2M; R_0603_1608Metric
U601: MCP96RL01T; QFN-20_EP_5x5_Pitch0.65mm

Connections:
+3.3VA: C601.2, C602.1, R601.1, U601.8 (VDD); also elsewhere on the board
/Display/I2C_SCL: U601.19 (SCL); also elsewhere on the board
/Display/I2C_SDA: U601.20 (SDA); also elsewhere on the board
GND: C601.1, C602.2, R602.1, R603.2, U601.1 (GND), U601.3 (GND), U601.5 (GND), U601.10 (GND), U601.13 (GND), U601.16 (ADDR), U601.17 (GND), U601.18 (GND); also elsewhere on the board
unnamed: J601.1, U601.2 (Vin+)
unnamed: J601.2, R603.1, U601.4 (Vin-)
unnamed: R601.2, R602.2, U601.6 (V_Sense)

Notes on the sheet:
I2C Address = 1100 000 = 0xC0

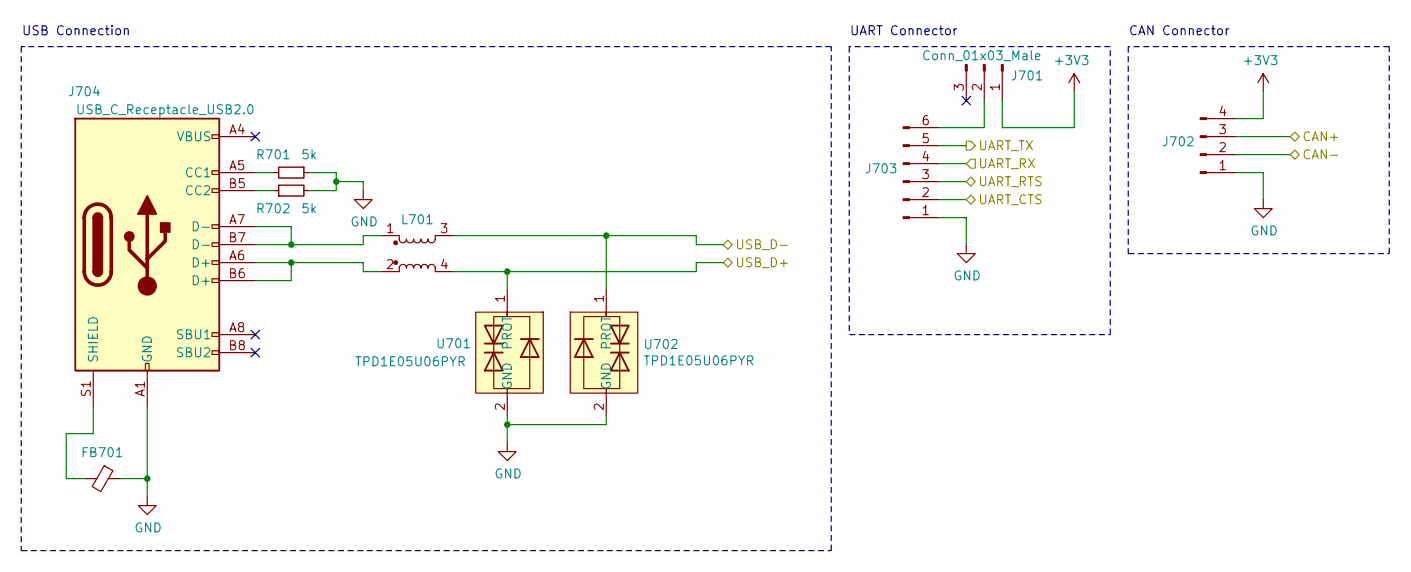
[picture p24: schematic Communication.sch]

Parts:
FB701: FerriteBead_Small; L_0603_1608Metric
J701: Conn_01x03_Male; PinHeader_1x03_P1.00mm_Vertical
J702: Microfit-4pin; PinHeader_2x02_P1.00mm_Vertical
J703: Conn_01x06_Male; PinHeader_1x06_P1.00mm_Vertical
J704: USB_C_Receptacle_USB2.0; USB_C_Receptacle_Amphenol_12401610E4-2A
L701: L_Coupled_Small_1324; 744231091
R701, R702: 5k; R_0603_1608Metric
U701, U702: TPD1E05U06PYR; D_0402_1005Metric

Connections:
/Communication/CAN+: J702.3; also elsewhere on the board
/Communication/CAN-: J702.2; also elsewhere on the board
/Communication/UART_CTS: J703.2; also elsewhere on the board
/Communication/UART_RTS: J703.3; also elsewhere on the board
/Communication/UART_RX: J703.4; also elsewhere on the board
/Communication/UART_TX: J703.5; also elsewhere on the board
/Communication/USB_D+: L701.4, U701.1 (PROT); also elsewhere on the board
/Communication/USB_D-: L701.3, U702.1 (PROT); also elsewhere on the board
GND: FB701.1, J702.1, J703.1, J704.A1 (GND), J704.A12 (GND), J704.B1 (GND), J704.B12 (GND), R701.1, R702.2, U701.2 (GND), U702.2 (GND); also elsewhere on the board
unnamed: FB701.2, J704.S1 (SHIELD)
unnamed: J701.2, J703.6
unnamed: J704.A4 (VBUS), J704.A9 (VBUS), J704.B4 (VBUS), J704.B9 (VBUS)
unnamed: J704.A5 (CC1), R701.2
unnamed: J704.A6 (D+), J704.B6 (D+), L701.2
unnamed: J704.A7 (D-), J704.B7 (D-), L701.1
unnamed: J704.B5 (CC2), R702.1

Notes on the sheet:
USB Connection
UART Connector
CAN Connector

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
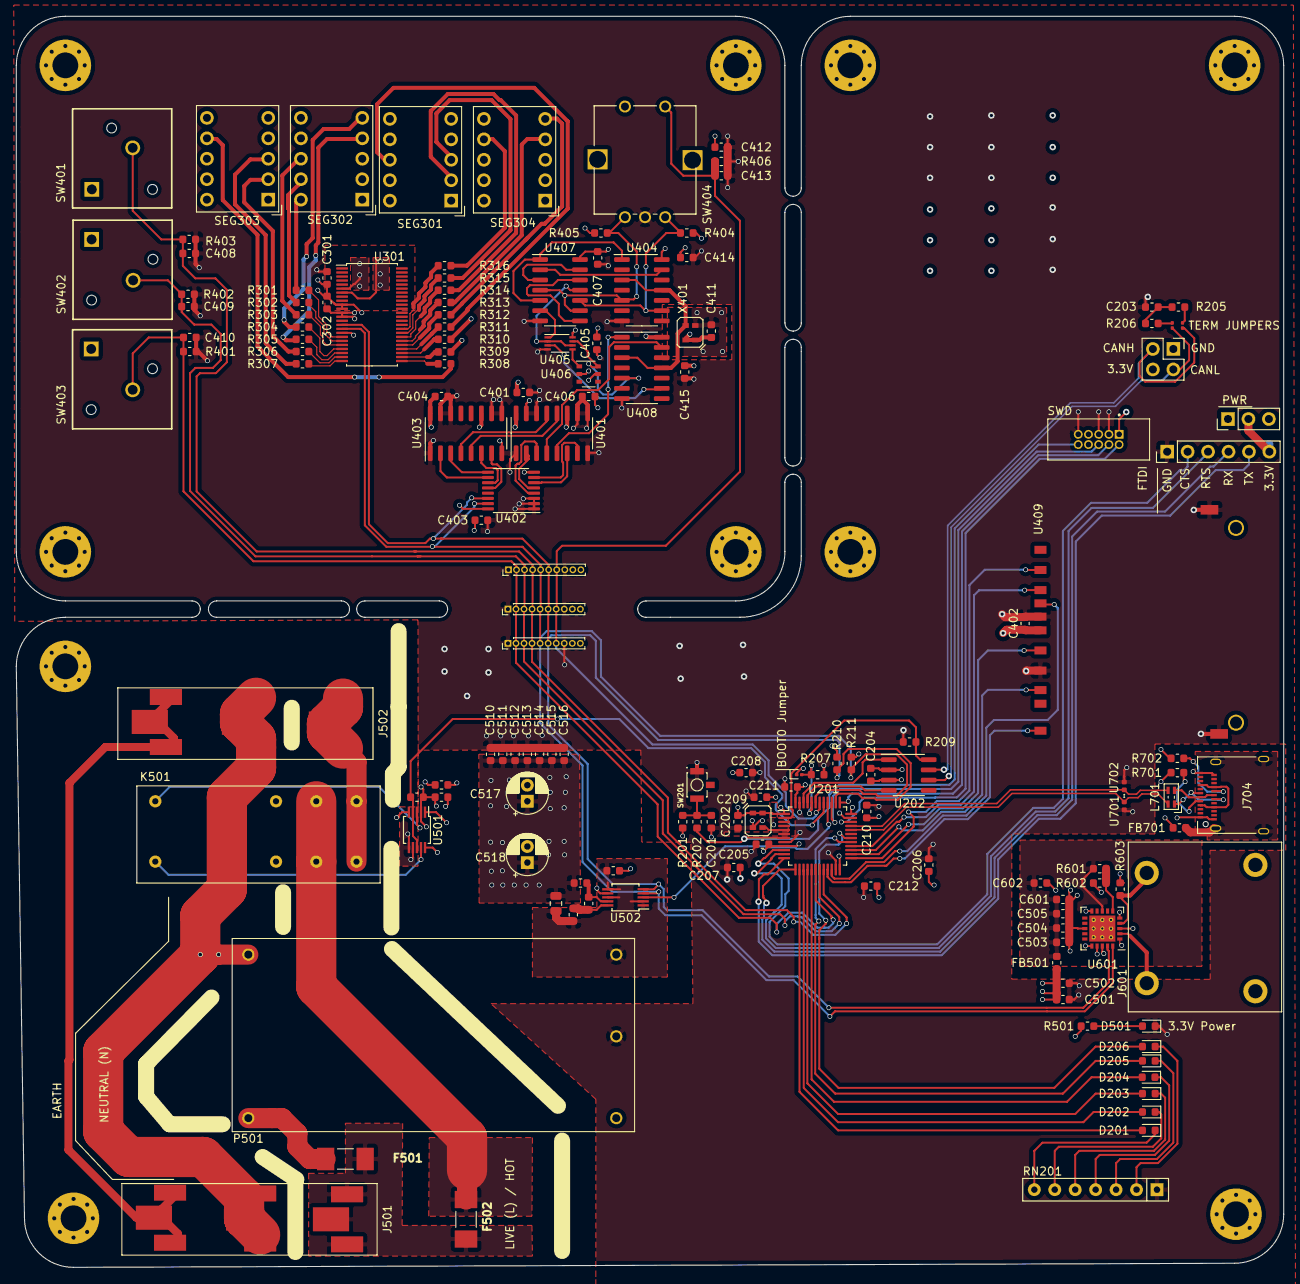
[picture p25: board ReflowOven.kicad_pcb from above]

Board: 4 copper layers, 157.5 x 155.4 mm, 143 parts (0 on the bottom side), 130 nets.

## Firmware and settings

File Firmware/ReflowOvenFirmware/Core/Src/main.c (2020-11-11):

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
/* Includes ------------------------------------------------------------------*/
#include "main.h"
#include "cmsis_os.h"

/* USER CODE BEGIN Includes */
#include "INA226_Driver.h"
#include "MCP96RL01T_Driver.h"
#include "SDCard_Driver.h"
#include "PCF8551ATT_Driver.h"
#include "TCA9534_Driver.h"
/* USER CODE END Includes */

CAN_HandleTypeDef hcan;

SMBUS_HandleTypeDef hsmbus1;

SPI_HandleTypeDef hspi2;

UART_HandleTypeDef huart2;

PCD_HandleTypeDef hpcd_USB_FS;

osThreadId defaultTaskHandle;
void SystemClock_Config(void);
static void MX_GPIO_Init(void);
static void MX_CAN_Init(void);
static void MX_I2C1_SMBUS_Init(void);
static void MX_SPI2_Init(void);
static void MX_USART2_UART_Init(void);
static void MX_USB_PCD_Init(void);
void StartDefaultTask(void const * argument);

/**
  * @brief  The application entry point.
  * @retval int
  */
int main(void)
{
  /* MCU Configuration--------------------------------------------------------*/

  /* Reset of all peripherals, Initializes the Flash interface and the Systick. */
  HAL_Init();

  /* Configure the system clock */
  SystemClock_Config();

  /* Initialize all configured peripherals */
  MX_GPIO_Init();
  MX_CAN_Init();
  MX_I2C1_SMBUS_Init();
  MX_SPI2_Init();
  MX_USART2_UART_Init();
  MX_USB_PCD_Init();
  /* USER CODE BEGIN RTOS_MUTEX */
  /* add mutexes, ... */
  /* USER CODE END RTOS_MUTEX */

  /* USER CODE BEGIN RTOS_SEMAPHORES */
  /* add semaphores, ... */
  /* USER CODE END RTOS_SEMAPHORES */

  /* USER CODE BEGIN RTOS_TIMERS */
  /* start timers, add new ones, ... */
  /* USER CODE END RTOS_TIMERS */

  /* USER CODE BEGIN RTOS_QUEUES */
  /* add queues, ... */
  /* USER CODE END RTOS_QUEUES */

  /* Create the thread(s) */
  /* definition and creation of defaultTask */
  osThreadDef(defaultTask, StartDefaultTask, osPriorityNormal, 0, 128);
  defaultTaskHandle = osThreadCreate(osThread(defaultTask), NULL);

  /* USER CODE BEGIN RTOS_THREADS */
  /* add threads, ... */
  /* USER CODE END RTOS_THREADS */

  /* Start scheduler */
  osKernelStart();

  /* We should never get here as control is now taken by the scheduler */
  /* Infinite loop */
  /* USER CODE BEGIN WHILE */
  while (1)
  {
    /* USER CODE END WHILE */

    /* USER CODE BEGIN 3 */
  }
  /* USER CODE END 3 */
}

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
/* USER CODE BEGIN Header_StartDefaultTask */
/**
  * @brief  Function implementing the defaultTask thread.
  * @param  argument: Not used
  * @retval None
  */
/* USER CODE END Header_StartDefaultTask */
void StartDefaultTask(void const * argument)
{
  /* USER CODE BEGIN 5 */
  /* Infinite loop */
  for(;;)
  {
    osDelay(1);
  }
  /* USER CODE END 5 */
}

/**
  * @brief  Period elapsed callback in non blocking mode
  * @note   This function is called  when TIM1 interrupt took place, inside
  * HAL_TIM_IRQHandler(). It makes a direct call to HAL_IncTick() to increment
  * a global variable "uwTick" used as application time base.
  * @param  htim : TIM handle
  * @retval None
  */
void HAL_TIM_PeriodElapsedCallback(TIM_HandleTypeDef *htim)
{
  if (htim->Instance == TIM1) {
    HAL_IncTick();
  }
}

/**
  * @brief  This function is executed in case of error occurrence.
  * @retval None
  */
void Error_Handler(void)
{
  /* USER CODE BEGIN Error_Handler_Debug */
  /* User can add his own implementation to report the HAL error return state */

  /* USER CODE END Error_Handler_Debug */
}

#ifdef  USE_FULL_ASSERT
/**
  * @brief  Reports the name of the source file and the source line number
  *         where the assert_param error has occurred.
  * @param  file: pointer to the source file name
  * @param  line: assert_param error line source number
  * @retval None
  */
void assert_failed(uint8_t *file, uint32_t line)
{
  /* USER CODE BEGIN 6 */
  /* User can add his own implementation to report the file name and line number,
     tex: printf("Wrong parameters value: file %s on line %d\r\n", file, line) */
  /* USER CODE END 6 */
}
#endif /* USE_FULL_ASSERT */

/************************ (C) COPYRIGHT STMicroelectronics *****END OF FILE****/

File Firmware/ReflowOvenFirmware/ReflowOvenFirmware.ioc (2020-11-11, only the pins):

Mcu.UserName=STM32F302CBTx
PA0.Signal=USART2_CTS
PA1.Signal=USART2_RTS
PA11.Signal=USB_DM
PA12.Signal=USB_DP
PA13.Signal=SYS_JTMS-SWDIO
PA14.Signal=SYS_JTCK-SWCLK
PA15.Signal=I2C1_SCL
PA2.Signal=USART2_TX
PA3.Signal=USART2_RX
PA4.GPIO_Label=DLED0
PA4.Signal=GPIO_Output
PA5.GPIO_Label=DLED1
PA5.Signal=GPIO_Output
PA6.GPIO_Label=DLED2
PA6.Signal=GPIO_Output
PA7.GPIO_Label=DLED3
PA7.Signal=GPIO_Output
PA8.GPIO_Label=DLED4
PA8.Signal=GPIO_Output
PA9.GPIO_Label=DLED5
PA9.Signal=GPIO_Output
PB0.GPIO_Label=SW1
PB0.Signal=GPIO_Input
PB1.GPIO_Label=SW2
PB1.Signal=GPIO_Input
PB10.GPIO_Label=SD_WR_PROT
PB10.Signal=GPIO_Input
PB11.GPIO_Label=SD_DET
PB11.Signal=GPIO_Input
PB12.Signal=SPI2_NSS
PB13.Signal=SPI2_SCK
PB14.Signal=SPI2_MISO
PB15.Signal=SPI2_MOSI
PB2.GPIO_Label=SW3
PB2.Signal=GPIO_Input
PB3.Signal=SYS_JTDO-TRACESWO
PB4.GPIO_Label=CURRENT_ALRT
PB4.Signal=GPIO_Input
PB5.GPIO_Label=RELAY_SET
PB5.Signal=GPIO_Output
PB6.GPIO_Label=ENC_SW
PB6.Signal=GPIO_Input
PB7.Signal=I2C1_SDA
PB8.Signal=CAN_RX
PB9.Signal=CAN_TX
PC13.GPIO_Label=CAN_SIL
PC13.Signal=GPIO_Output
PF0-OSC_IN.Signal=RCC_OSC_IN

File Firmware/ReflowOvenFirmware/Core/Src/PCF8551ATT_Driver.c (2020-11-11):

#include "PCF8551ATT_Driver.h"

static uint8_t DEVICE_ADDR;
static uint8_t WriteRegister_PCF8551(uint8_t addr, uint8_t reg, uint8_t value, SMBUS_HandleTypeDef *I2C);
static uint8_t ReadRegister_PCF8551(uint8_t addr, uint8_t reg, uint8_t *output, SMBUS_HandleTypeDef *I2C);
static uint8_t WriteMultipleRegister_PCF8551(uint8_t addr, uint8_t reg, uint8_t *value, uint8_t num, SMBUS_HandleTypeDef *I2C);

uint8_t Init_PCF8551(PCF8551_Config *configuration, SMBUS_HandleTypeDef *I2C)
{
    uint8_t status = PCF8551_SUCCESS;
    DEVICE_ADDR = configuration->DEV_ADDR;
    uint8_t devCtlReg = !!configuration->CLOCK_OUT_ENABLED;
    devCtlReg |= configuration->INT_OSC_ENABLED << 1;
    devCtlReg |= configuration->FRAME_FREQ << 2;
    status &= WriteRegister_PCF8551(DEVICE_ADDR, PCF8551_DEVICE_CTL_REG, devCtlReg, I2C);
    uint8_t displayCtlReg = configuration->DISPLAY_ENABLE;
    displayCtlReg |= configuration->BIAS_MODE << 1;
    displayCtlReg |= configuration->DRIVE_MODE << 2;
    displayCtlReg |= configuration->BOOST << 4;
    status &= WriteRegister_PCF8551(DEVICE_ADDR, PCF8551_DISPLAY_CTL_1, displayCtlReg, I2C);
    displayCtlReg = configuration->INVERSION_MODE;
    displayCtlReg |= configuration->BLINK << 1;
    status &= WriteRegister_PCF8551(DEVICE_ADDR, PCF8551_DISPLAY_CTL_2, displayCtlReg, I2C);
    return status;
}

uint8_t WriteSegment_PCF8551(PCF8551_COM_PORT port, PCF8551_SEG segment, uint8_t value, SMBUS_HandleTypeDef *I2C)
{
    uint8_t reg = (port + 1) * (uint8_t) PCF8551_COM0_SEG0 + (uint8_t) segment;
    uint8_t status = WriteRegister_PCF8551(DEVICE_ADDR, reg, value, I2C);
    return status;
}

uint8_t WritePort_PCF8551(PCF8551_COM_PORT port, uint32_t value, SMBUS_HandleTypeDef *I2C)
{
    uint8_t buffer[4];
    buffer[0] = value;
    buffer[1] = value >> 8;
    buffer[2] = value >> 16;
    buffer[3] = value >> 24;

    uint8_t reg = (port + 1) * (uint8_t) PCF8551_COM0_SEG0;

    return WriteMultipleRegister_PCF8551(DEVICE_ADDR, reg, buffer, 4, I2C);
}

uint32_t GetPortValueFromDigits(uint8_t digit0, uint8_t digit1, uint8_t digit2, uint8_t digit3, uint8_t dots)
{   
    uint32_t portValue;
    portValue = GetSegmentValueFromDigit(digit0, 0);
    portValue |= GetSegmentValueFromDigit(digit1, 0) << 8;
    portValue |= GetSegmentValueFromDigit(digit2, 0) << 16;
    portValue |= GetSegmentValueFromDigit(digit3, 0) << 24;
    
    return portValue;
}

uint32_t GetPortValueFromCharacters(char digit0, char digit1, char digit2, char digit3, char dots) 
{
    uint32_t portValue;
    portValue = GetSegmentValueFromCharacter(digit0, 0);
    portValue |= GetSegmentValueFromCharacter(digit1, 0) << 8;
    portValue |= GetSegmentValueFromCharacter(digit2, 0) << 16;
    portValue |= GetSegmentValueFromCharacter(digit3, 0) << 24;
    
    return portValue;
}

uint8_t WriteRegister_PCF8551(uint8_t addr, uint8_t reg, uint8_t value, SMBUS_HandleTypeDef *I2C) 
{
    uint8_t buffer[1];
    buffer[0] = value;

    HAL_StatusTypeDef status = HAL_OK;
    while (HAL_I2C_IsDeviceReady(I2C, addr, PCF8551_READY_TRIALS, PCF8551_Timeout) != HAL_OK);
    
    status = HAL_I2C_Mem_Write(I2C, addr, reg, I2C_MEMADD_SIZE_8BIT, buffer, 1, PCF8551_Timeout);
    
    if (status == HAL_OK)
    {
        return PCF8551_SUCCESS;
    }
    return PCF8551_FAILURE;
}

uint8_t WriteMultipleRegister_PCF8551(uint8_t addr, uint8_t reg, uint8_t *value, uint8_t num, SMBUS_HandleTypeDef *I2C) 
{

    HAL_StatusTypeDef status = HAL_OK;
    while (HAL_I2C_IsDeviceReady(I2C, addr, PCF8551_READY_TRIALS, PCF8551_Timeout) != HAL_OK);
    
    status = HAL_I2C_Mem_Write(I2C, addr, reg, I2C_MEMADD_SIZE_8BIT, value, num, PCF8551_Timeout);
    
    if (status == HAL_OK)
    {
        return PCF8551_SUCCESS;
    }
    return PCF8551_FAILURE;
}

uint8_t ReadRegister_PCF8551(uint8_t addr, uint8_t reg, uint8_t *output, SMBUS_HandleTypeDef *I2C) 
{
    uint8_t buffer[1];

    HAL_StatusTypeDef status = HAL_OK;
    while (HAL_I2C_IsDeviceReady(I2C, addr, PCF8551_READY_TRIALS, PCF8551_Timeout) != HAL_OK);
    
    status = HAL_I2C_Mem_Read(I2C, addr, reg, I2C_MEMADD_SIZE_8BIT, buffer, 1, PCF8551_Timeout);
    *output = buffer[0];

    if (status == HAL_OK)
    {
        return PCF8551_SUCCESS;
    }
    return PCF8551_FAILURE;
}

uint8_t GetSegmentValueFromDigit(uint8_t digit, uint8_t invertOutput)
{
    uint8_t segVal = 0x00;
    switch(digit) {
        case 1:
            segVal = 0x00;
            break;
        case 2:
            segVal = 0x00;
            break;
        case 3:
            segVal = 0x00;
            break;
        case 4:
            segVal = 0x00;
            break;
        case 5:
            segVal = 0x00;
            break;
        case 6:
            segVal = 0x00;
            break;
        case 7:
            segVal = 0x00;
            break;
        case 8:
            segVal = 0x00;
            break;
        case 9:
            segVal = 0x00;
            break;
    }
    if (invertOutput) {
        return ~segVal;
    }
    return segVal;
}
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

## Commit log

2020-10-26 Initial commit, no firmware
    [10067847-001RLF.stp, 277.SLDPRT, 277.stp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]
2020-10-26 Updated Repo
    [10067847-001RLF.stp, 277.stp, 3220-10-0100.stp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]

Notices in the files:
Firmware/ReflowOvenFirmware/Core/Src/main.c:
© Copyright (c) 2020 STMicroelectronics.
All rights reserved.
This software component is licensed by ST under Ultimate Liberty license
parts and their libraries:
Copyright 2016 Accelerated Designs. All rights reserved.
